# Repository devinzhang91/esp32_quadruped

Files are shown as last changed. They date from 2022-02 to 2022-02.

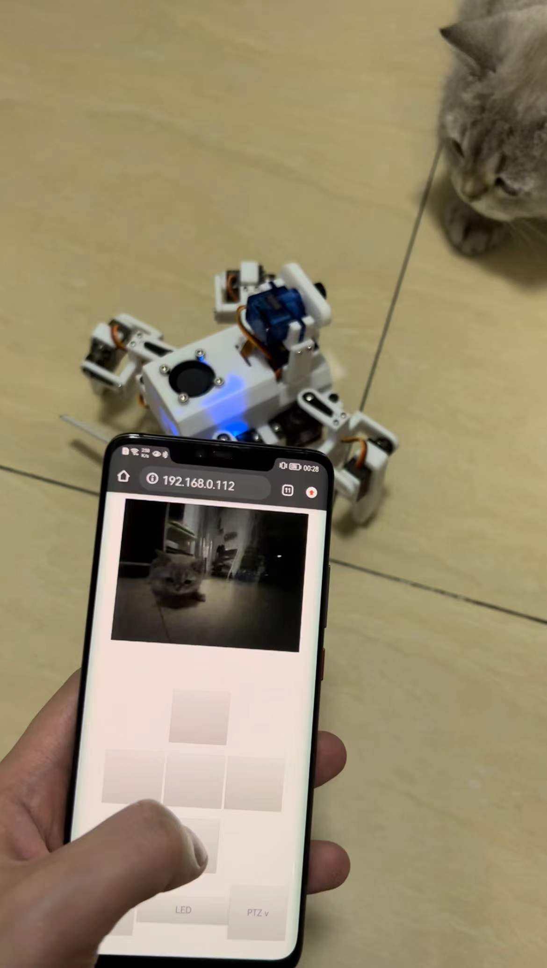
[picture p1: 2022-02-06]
pic/pic2.jpg

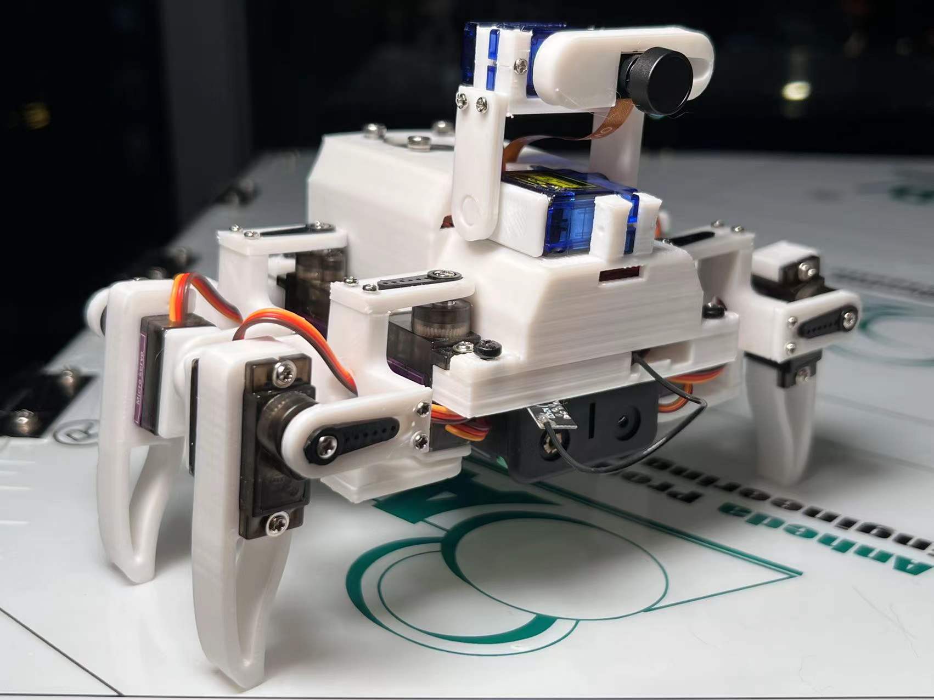
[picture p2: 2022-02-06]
pic/pic1.jpg

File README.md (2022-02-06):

# esp32_quadruped
## Summary

esp32 quadruped robot with arduino

Using 3D-printer an build it !

After assemble

## Details

### About Anruino

1. Prepare the ESP32 development environment

2. install lib: Adafruit_SSD1306, MPU6050 (by Electronic Cats), Adafruit_PWM_Servo_Driver_Library
3. Modify YOUR SSID and PASSWD in the code
4. Connect USB , hold the pin0 and upload
5.  Reset it and open the monitor, get this device IP, (esp32 work with station mode)
6.  Open browser with IP, you may see the camera image.

Contrl with web view

### About pcb

you may make a PCB circuit board proofing, and you may perpar :

1. servo : mg90s *10*
2. esp32-cam board
3. ov2640 (fpc 15cm at least)
4. battery: 18650* 2
5. parallel connection battery holder
6. 5V fan （2.5cm*2.5cm ）

PCB circuit board BOM:

1. power: FP6276*2
2. gyroscope : MPU6050
3. servo control IC：pca9685
4. USB to UART IC : ch340N
5. charge IC: TP4056
6. Thermal Camer : MLX90640 （Not necessary）
7. OLED : SSD1306 （Not necessary）
8. External antenna （Not necessary）

Screw：

1. M1.7*8   x50
2. M4*10    x4
3.  M3*10   x10
4. M3*35   x4
5. M3 Nut  x2
6. and so on ~

### About 3D object:

https://www.thingiverse.com/thing:5232362

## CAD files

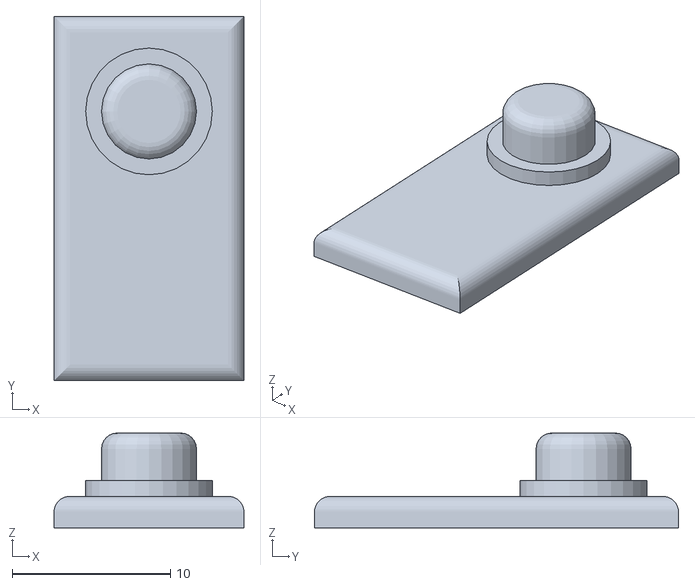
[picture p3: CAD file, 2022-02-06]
stl/leg_5.stl
12.0 x 23.0 x 6.00

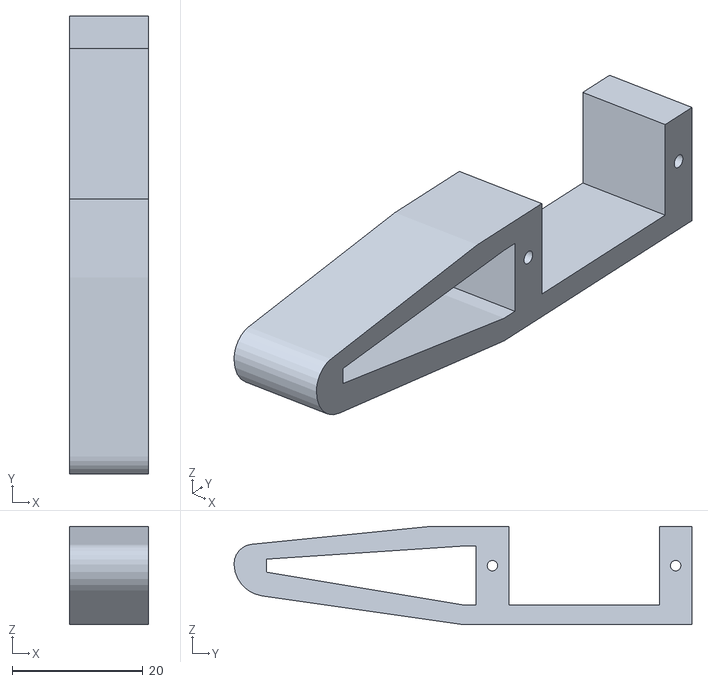
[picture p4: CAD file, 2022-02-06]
stl/leg_3.stl
12.0 x 70.0 x 15.0

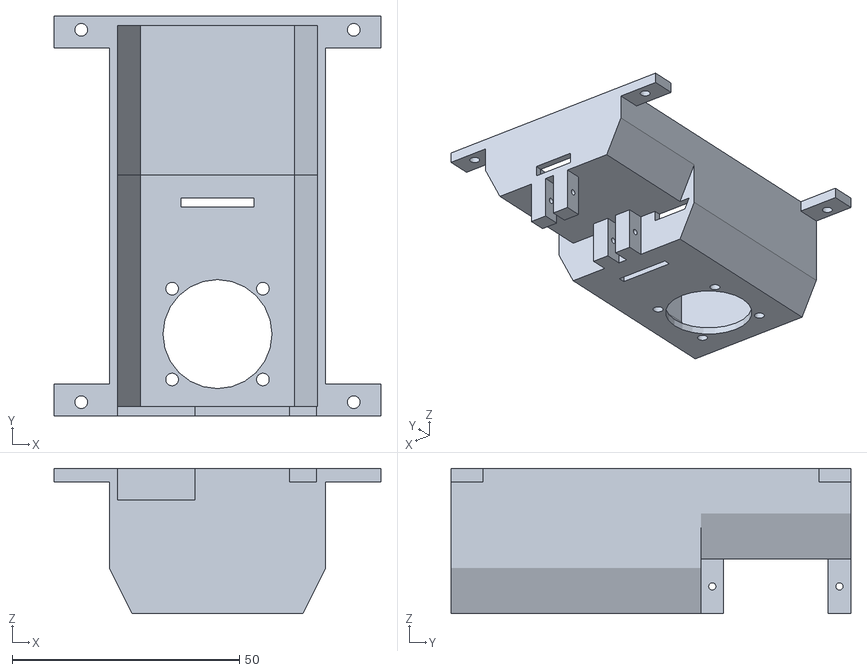
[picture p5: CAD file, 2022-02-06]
stl/body_buttom.stl
72.0 x 88.0 x 32.0

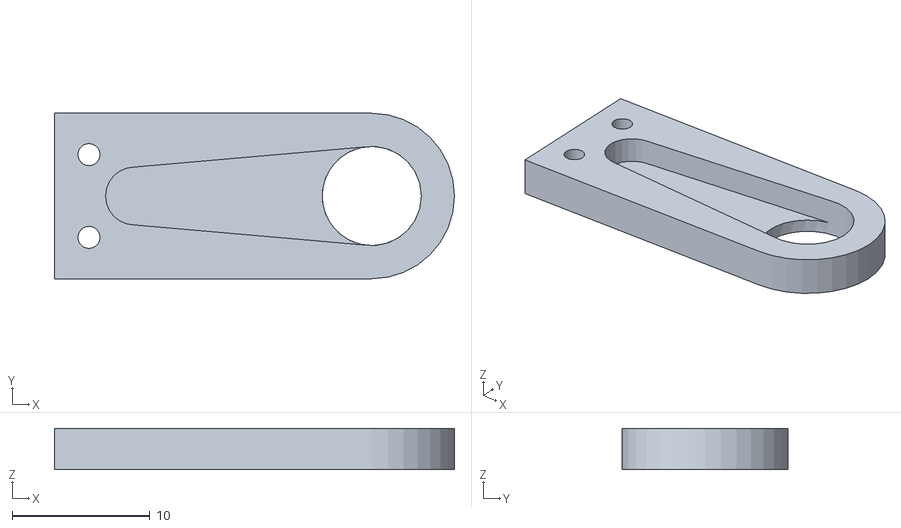
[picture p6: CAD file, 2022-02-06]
stl/leg_1.stl
29.0 x 12.0 x 3.00

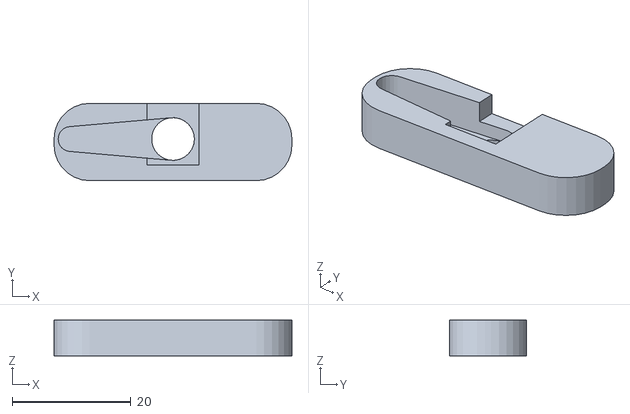
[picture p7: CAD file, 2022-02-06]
stl/cam.stl
40.0 x 13.0 x 6.00

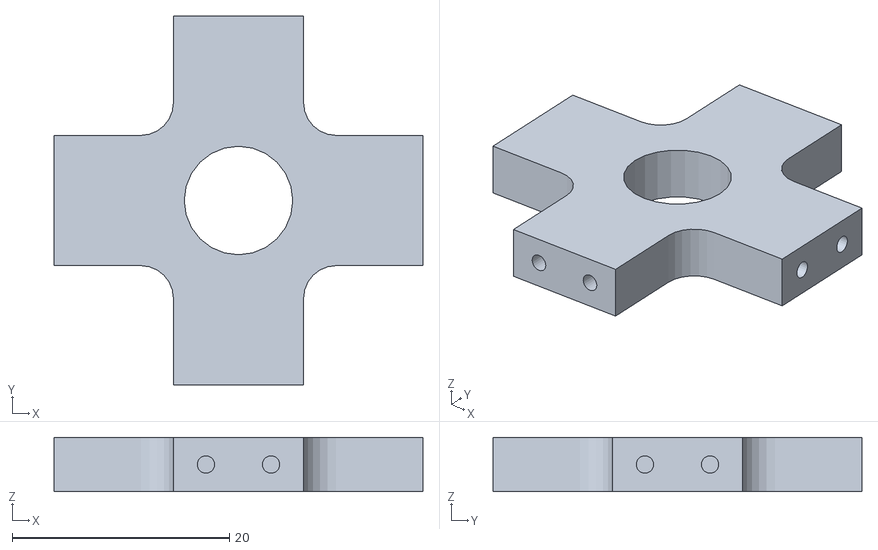
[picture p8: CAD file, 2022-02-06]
stl/leg_4_small.stl
34.0 x 34.0 x 5.00

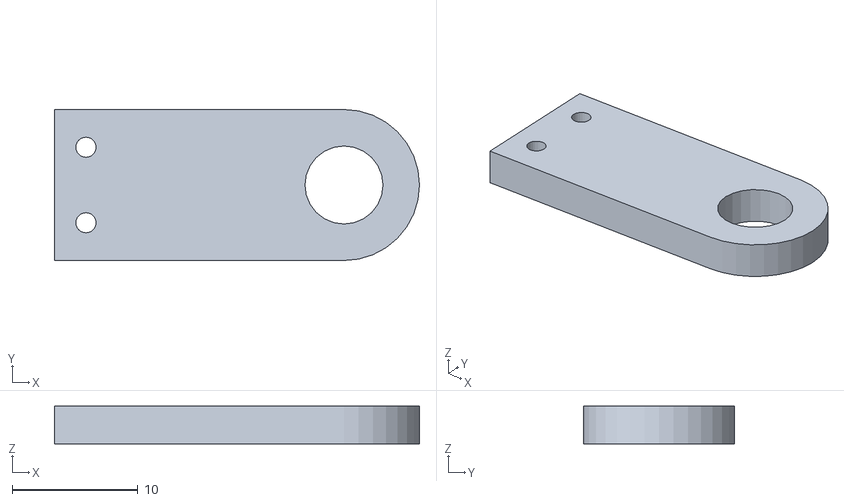
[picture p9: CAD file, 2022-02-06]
stl/leg_2.stl
29.0 x 12.0 x 3.00

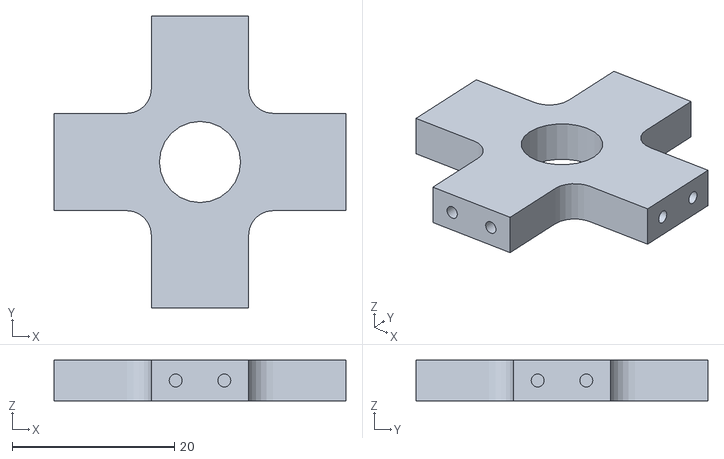
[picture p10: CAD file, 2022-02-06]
stl/leg_4_large.stl
36.0 x 36.0 x 5.00

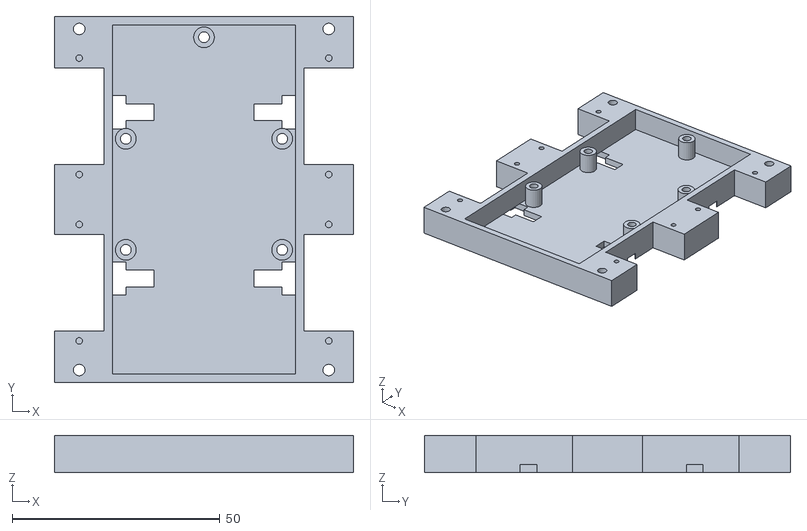
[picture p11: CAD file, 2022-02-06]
stl/body_up.stl
72.0 x 88.0 x 9.00

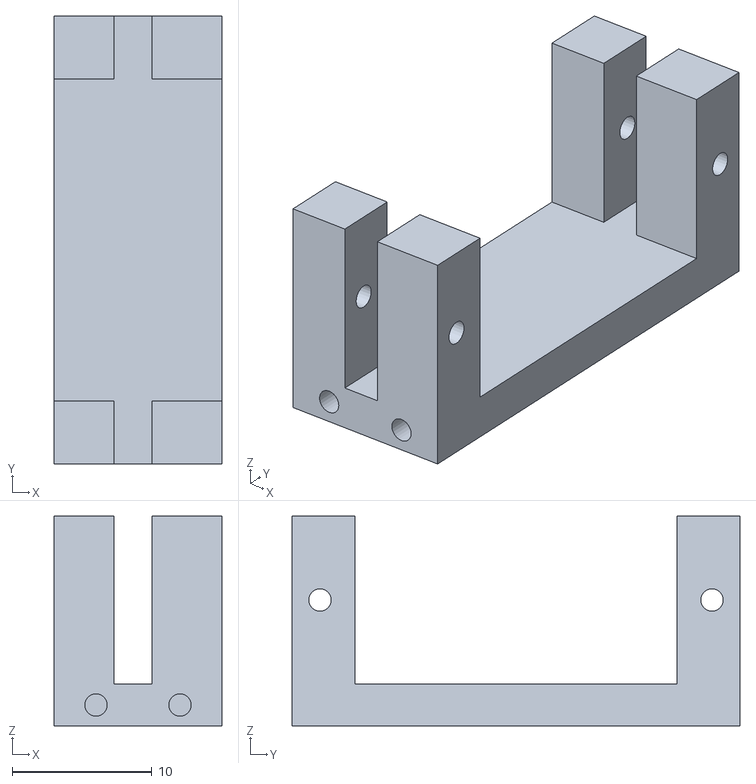
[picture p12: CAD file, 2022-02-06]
stl/ptz.stl
12.0 x 32.0 x 15.0

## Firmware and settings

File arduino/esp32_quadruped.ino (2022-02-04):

#include "esp_camera.h"
#include <WiFi.h>
#include <Wire.h>
#include <Adafruit_GFX.h>
#include <Adafruit_SSD1306.h>

#include "esp_http_server.h"
#include "esp_timer.h"
#include "img_converters.h"
#include "camera_pins.h"
#include "Esp.h"
#include "pca_action.h"
#include "gyroscope.h"

#define I2C_SDA 14 
#define I2C_SCL 15 
#define SCREEN_WIDTH 128 // OLED display width, in pixels
#define SCREEN_HEIGHT 64 // OLED display height, in pixels
#define OLED_RESET     13 // Reset pin # (or -1 if sharing Arduino reset pin)
#define SCREEN_ADDRESS 0x3C ///< See datasheet for Address;0x3C


const char* ssid = "YOUR SSID";
const char* password = "YOUR PASSWD";

const int led = 4;

void startCameraServer();

void init_camera(void){
  camera_config_t config;
  config.ledc_channel = LEDC_CHANNEL_0;
  config.ledc_timer = LEDC_TIMER_0;
  config.pin_d0 = Y2_GPIO_NUM;
  config.pin_d1 = Y3_GPIO_NUM;
  config.pin_d2 = Y4_GPIO_NUM;
  config.pin_d3 = Y5_GPIO_NUM;
  config.pin_d4 = Y6_GPIO_NUM;
  config.pin_d5 = Y7_GPIO_NUM;
  config.pin_d6 = Y8_GPIO_NUM;
  config.pin_d7 = Y9_GPIO_NUM;
  config.pin_xclk = XCLK_GPIO_NUM;
  config.pin_pclk = PCLK_GPIO_NUM;
  config.pin_vsync = VSYNC_GPIO_NUM;
  config.pin_href = HREF_GPIO_NUM;
  config.pin_sscb_sda = SIOD_GPIO_NUM;
  config.pin_sscb_scl = SIOC_GPIO_NUM;
  config.pin_pwdn = PWDN_GPIO_NUM;
  config.pin_reset = RESET_GPIO_NUM;
  config.xclk_freq_hz = 20000000;
  config.pixel_format = PIXFORMAT_JPEG;
  //init with high specs to pre-allocate larger buffers
  if(psramFound()){
    config.frame_size = FRAMESIZE_UXGA;
    config.jpeg_quality = 10;
    config.fb_count = 2;
  } else {
    config.frame_size = FRAMESIZE_SVGA;
    config.jpeg_quality = 12;
    config.fb_count = 1;
  }

#if defined(CAMERA_MODEL_ESP_EYE)
  pinMode(13, INPUT_PULLUP);
  pinMode(14, INPUT_PULLUP);
#endif

  // camera init
  esp_err_t err = esp_camera_init(&config);
  if (err != ESP_OK) {
    Serial.printf("Camera init failed with error 0x%x", err);
    return;
  }

  sensor_t * s = esp_camera_sensor_get();
  //drop down frame size for higher initial frame rate
  s->set_framesize(s, FRAMESIZE_QVGA);

#if defined(CAMERA_MODEL_M5STACK_WIDE)
  s->set_vflip(s, 1);
  s->set_hmirror(s, 1);
#endif
}

void setup(void) {
    pinMode(led, OUTPUT);
    digitalWrite(led, 0);

    Serial.begin(115200);

    Wire.begin(I2C_SDA, I2C_SCL);
    Adafruit_SSD1306 display(SCREEN_WIDTH, SCREEN_HEIGHT, &Wire, OLED_RESET);

    if(!display.begin(SSD1306_SWITCHCAPVCC, SCREEN_ADDRESS)) {
        Serial.println(F("SSD1306 allocation failed"));
    }
    Serial.println(F("SSD1306 allocation successed."));
    display.display();
    delay(1000); 
    display.setTextSize(1);
    display.setTextColor(SSD1306_WHITE);
    display.clearDisplay();
    display.setCursor(0,0);
    display.print(ssid);
    display.display(); // actually display all of the above

    if(psramInit()){
        Serial.println("PSRAM enable!");
    }

    WiFi.begin(ssid, password);
    // Wait for connection
    while (WiFi.status() != WL_CONNECTED) {
        delay(500);
        Serial.print(".");
        digitalWrite(led, HIGH);
        delay(10);
        digitalWrite(led, LOW);
    }
    Serial.println("");
    Serial.print("Connected to ");
    Serial.println(ssid);
    Serial.print("IP address: ");
    Serial.println(WiFi.localIP());

    init_camera();
    startCameraServer();
    Serial.println("HTTP server started");

    // WiFi.mode(WIFI_STA);
    // WiFi.begin(ssid, password);
    // Serial.println("");

    // while (WiFi.status() != WL_CONNECTED) {
    //     delay(500);
    //     Serial.print(".");
    // }
    // Serial.println("");
    // Serial.print("Connected to ");
    // Serial.println(ssid);
    // Serial.print("IP address: ");
    // Serial.println(WiFi.localIP());
    display.setCursor(0,8);
    display.print(WiFi.localIP().toString());
    display.display(); // actually display all of the above

    
    initGyro();
    init_pac9685();
    Serial.println("Mechanical parts started");

}

void loop(void) {
    // put your main code here, to run repeatedly:
    // quad_right_rotation();
    // delay(500);
}

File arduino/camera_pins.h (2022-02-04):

#define CAMERA_MODEL_AI_THINKER

#if defined(CAMERA_MODEL_WROVER_KIT)
#define PWDN_GPIO_NUM    -1
#define RESET_GPIO_NUM   -1
#define XCLK_GPIO_NUM    21
#define SIOD_GPIO_NUM    26
#define SIOC_GPIO_NUM    27

#define Y9_GPIO_NUM      35
#define Y8_GPIO_NUM      34
#define Y7_GPIO_NUM      39
#define Y6_GPIO_NUM      36
#define Y5_GPIO_NUM      19
#define Y4_GPIO_NUM      18
#define Y3_GPIO_NUM       5
#define Y2_GPIO_NUM       4
#define VSYNC_GPIO_NUM   25
#define HREF_GPIO_NUM    23
#define PCLK_GPIO_NUM    22

#elif defined(CAMERA_MODEL_ESP_EYE)
#define PWDN_GPIO_NUM    -1
#define RESET_GPIO_NUM   -1
#define XCLK_GPIO_NUM    4
#define SIOD_GPIO_NUM    18
#define SIOC_GPIO_NUM    23

#define Y9_GPIO_NUM      36
#define Y8_GPIO_NUM      37
#define Y7_GPIO_NUM      38
#define Y6_GPIO_NUM      39
#define Y5_GPIO_NUM      35
#define Y4_GPIO_NUM      14
#define Y3_GPIO_NUM      13
#define Y2_GPIO_NUM      34
#define VSYNC_GPIO_NUM   5
#define HREF_GPIO_NUM    27
#define PCLK_GPIO_NUM    25

#elif defined(CAMERA_MODEL_M5STACK_PSRAM)
#define PWDN_GPIO_NUM     -1
#define RESET_GPIO_NUM    15
#define XCLK_GPIO_NUM     27
#define SIOD_GPIO_NUM     25
#define SIOC_GPIO_NUM     23

#define Y9_GPIO_NUM       19
#define Y8_GPIO_NUM       36
#define Y7_GPIO_NUM       18
#define Y6_GPIO_NUM       39
#define Y5_GPIO_NUM        5
#define Y4_GPIO_NUM       34
#define Y3_GPIO_NUM       35
#define Y2_GPIO_NUM       32
#define VSYNC_GPIO_NUM    22
#define HREF_GPIO_NUM     26
#define PCLK_GPIO_NUM     21

#elif defined(CAMERA_MODEL_M5STACK_WIDE)
#define PWDN_GPIO_NUM     -1
#define RESET_GPIO_NUM    15
#define XCLK_GPIO_NUM     27
#define SIOD_GPIO_NUM     22
#define SIOC_GPIO_NUM     23

#define Y9_GPIO_NUM       19
#define Y8_GPIO_NUM       36
#define Y7_GPIO_NUM       18
#define Y6_GPIO_NUM       39
#define Y5_GPIO_NUM        5
#define Y4_GPIO_NUM       34
#define Y3_GPIO_NUM       35
#define Y2_GPIO_NUM       32
#define VSYNC_GPIO_NUM    25
#define HREF_GPIO_NUM     26
#define PCLK_GPIO_NUM     21

#elif defined(CAMERA_MODEL_AI_THINKER)
#define PWDN_GPIO_NUM     32
#define RESET_GPIO_NUM    -1
#define XCLK_GPIO_NUM      0
#define SIOD_GPIO_NUM     26
#define SIOC_GPIO_NUM     27

#define Y9_GPIO_NUM       35
#define Y8_GPIO_NUM       34
#define Y7_GPIO_NUM       39
#define Y6_GPIO_NUM       36
#define Y5_GPIO_NUM       21
#define Y4_GPIO_NUM       19
#define Y3_GPIO_NUM       18
#define Y2_GPIO_NUM        5
#define VSYNC_GPIO_NUM    25
#define HREF_GPIO_NUM     23
#define PCLK_GPIO_NUM     22

#else
#error "Camera model not selected"
#endif

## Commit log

2022-02-04 Add arduino project and code.
2022-02-06 Add pcb files.
    [quadrupe.PcbDoc, quadrupe.SchDoc]
2022-02-06 Add 3D object (.stl) files.
    [body_buttom.stl, body_up.stl, cam.stl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]
